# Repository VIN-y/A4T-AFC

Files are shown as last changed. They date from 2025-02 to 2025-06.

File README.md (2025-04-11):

[][cc-by-nc-sa]

# A4T-AFC: [A]nother [4]010 [T]oolhead - [A]nother [F]ilament [C]utter

## BETA Release

A toolhead cutter mod from: ko-fi (https://ko-fi.com/southash1) [SouthAsh1](https://ko-fi.com/southash1)

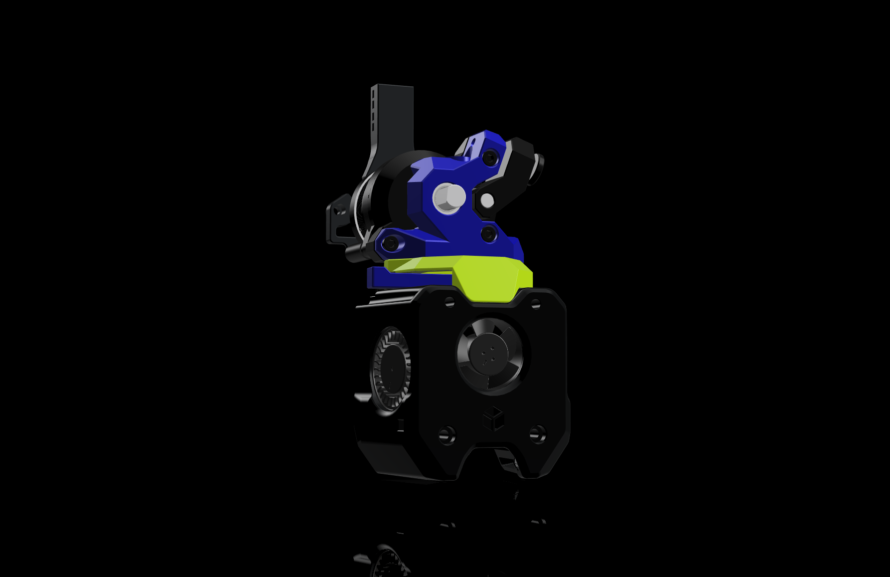
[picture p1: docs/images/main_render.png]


<br/> 
A filament cutter mod designed around the A4T that is designed by DW-Tas. Focused on keeping the original size as close as possible while still keeping the build relatively simple. <br/><br/>

I will try to get the board mounts made soon.

> [!NOTE] 
> ### Total WIP<br/>
> This mod is still a WIP and some things may change, most changes will be minor. Also the CAD will come out later.<br/>

<br/><br/>

> [!WARNING]
> ### Very Sharp  
> This project requires you to modify very sharp objects. I will cover how to handle these when I get to finishing the instalation instructions very soon. 

<br/>

## Bill of Materials (BOM)
***`*Not including stock A4T hardware`***
| Qty | Item | Notes |
| --- | --- | --- |
| 1 | Bambu Blade | This mod uses a Bambu Labs filament cutter blade that has been stripped of its plastic. <a href="https://us.store.bambulab.com/products/replacement-filament-cutter?_pos=1&_ss=r">Bambu Blade</a>|
| 1 | 0.5x4x15 Spring | Any spring that is 4mm in diameter and no longer than 15mm should work your milage may vary for cutting force needed.|
| 1 | M2 x 4 FHCS | Keeps the blade from sliding in and out.|
| 2 | M2 `Flange` Heatsets | This is the bread and butter of tolerances for the build. <br/> Recommended: ---<a href="https://www.digikey.com/en/products/detail/tri-star-industries-inc/HM20X157C/14205393">Digikey</a> <br/> Alternative: --------<a href="https://www.aliexpress.us/item/3256805733805809.html">Ali Express</a>|
| 2 | 3 x 10 mm pin | Pivot pins for the `Link`<br/> Example: <a href="https://www.amazon.com/uxcell-Stainless-Cylindrical-Support-Elements/dp/B07Y58VWDW?th=1">Amazon</a>|
| 2 | 3 x 12 mm pin | Pivot pins for the `Cutter Arm` and `Blade Holder`<br/> Example: <a href="https://www.amazon.com/uxcell-Stainless-Cylindrical-Support-Elements/dp/B07Y58CFYF?th=1">Amazon</a>|
| 4 | 3 ID x 5 OD x 5 H mm Sleeve Bearings | Bearing surfaces for the pins to guide on. <br/> Example: <a href="https://www.amazon.com/uxcell-Bearings-Wrapped-Bushings-Machinery/dp/B0CW31938R?th=1">Amazon</a>|
| 1 | M3 Threaded Heat Insert | Standard Voron spec: M3 x 5 x 4|
| 1 | M3 x 6 SHCS | Holds the `Extruder Adapter` on.|
| | **OPTIONAL** |
| 4 | M2.5 x 8 / M2.5 x 12 FHCS | To mount the hotend for ONLY the UHF options. 12mm length if you are using the spacer.|
| | **Extruder Mounting Screws** |
| | WWBMG, Orbiter | 2-`M3x18 SHCS`|
| | WWG2 | 1-`M3x20 SHCS` 1-`M3x18 SHCS`|
| | Sherpa | 2-`M3x24 BHCS` Sorry but you need to file/sand down 1mm on 25mm screws.|

## Printing parts
### Print settings
> [!WARNING]<br/>
> Recommended to print the `Link` and `Blade Holder` with 100% infill.<br/>

Parts are meant to be printed in 0.2mm layer heights, 0.25mm first layer should be OK. Other layer heights will cause the built-in supports to fail or fuse to the printed part.<br/>
Print settings will depend on your printer setup / filament used / phase of the moon/etc.<br/>
The parts are not pre-scaled for any particular filament type. You will need to tune the filament you use for correct shrinkage compensation to get good results. Development was done with multiple brands of ASA and ASA-CF filaments (each individually tuned).<br/>

General voron-like settings are a good starting point for 0.4mm wall widths (four walls, 5 top/bottom layers and 40% infill).<br/>

⚠ If you have any under-extrusion you will have problems with the parts stretching and not keeping rigidity. ⚠

(Similar rules of A4T applies here so I kind of copied and pasted, sue me...)

## Assembly
### Assembly Steps

These istructions should be followed in conjunction with original <a href="https://github.com/Armchair-Heavy-Industries/A4T">A4T instructions</a>.

:information_source: CW2 and Tap users have to build the toolhead on the printer, Xol Carriage users can build off the printer.
| <center>Notes</center> | Images|
| --- | :-----: |
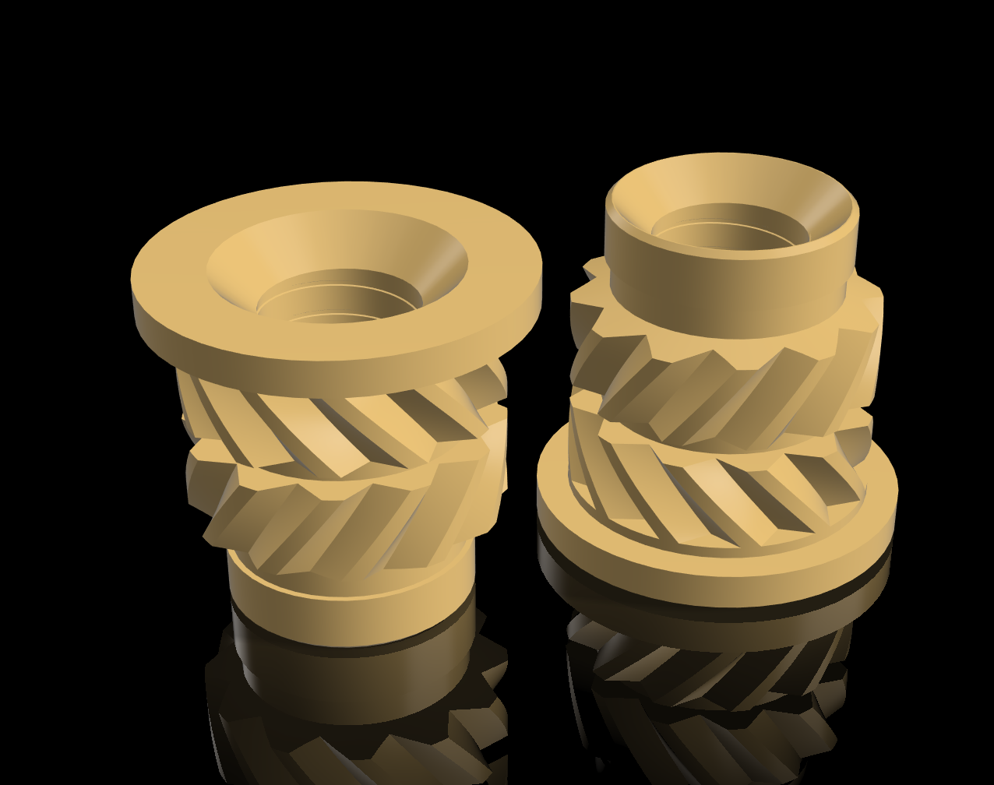
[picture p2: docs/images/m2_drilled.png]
| Prep the M2 inserts for install by drilling them out with a 5/64 or 2mm Drill Bit, then in one of them chamfer the top and the other chamfer the bottom. | <br/> |
| **Preping the Blade Holder** |
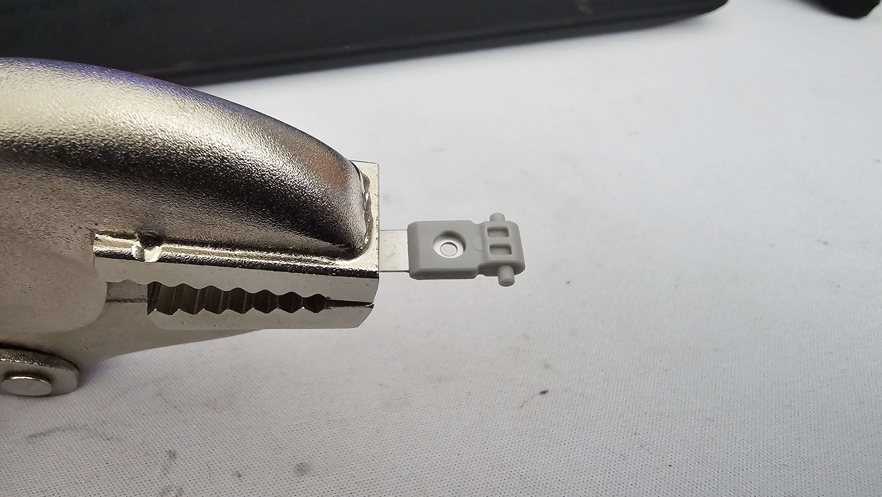
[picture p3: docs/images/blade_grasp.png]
| Start by using a pair of vise grips, a pair of pliars, or a vise that can firmly grasp the blade and prevent it from moving. | <br/> |
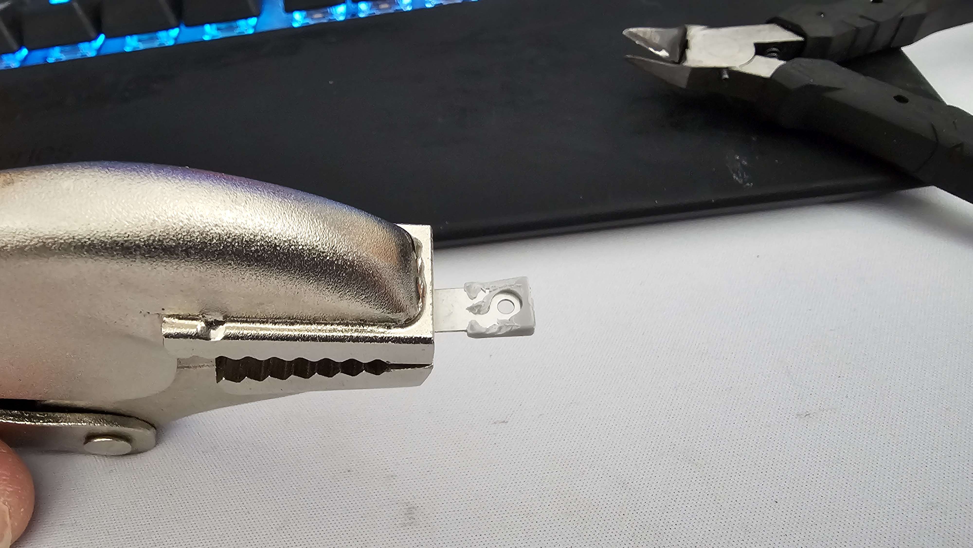
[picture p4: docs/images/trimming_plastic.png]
| Next, using flush cutters, cut the tab on the back `⚠⚠ flying parts ⚠⚠` and start triming the plastic off one side. | <br/> |
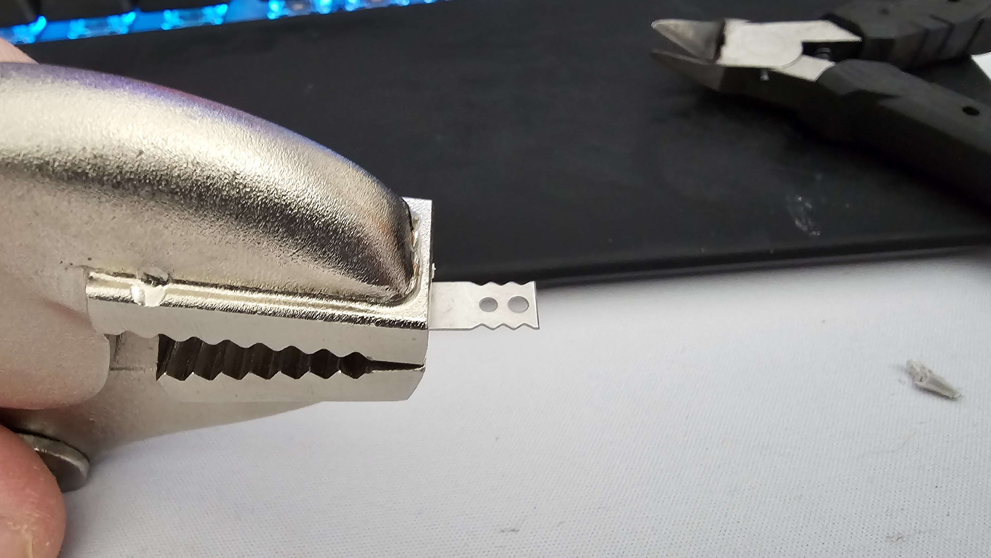
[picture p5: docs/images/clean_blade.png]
| When you get enough plastic off one side then the other side can just be pulled off then you will get a clean blade ready for install. | <br/> |
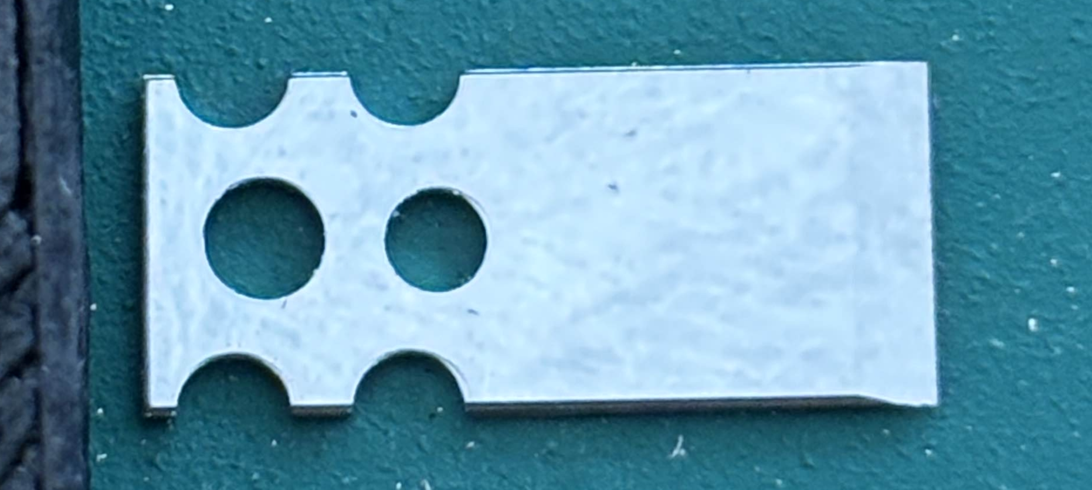
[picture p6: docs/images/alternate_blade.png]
| There are alternate types of Bambu blades that may differ depending on where on the globe you buy them on, they will still work. | <br/> |
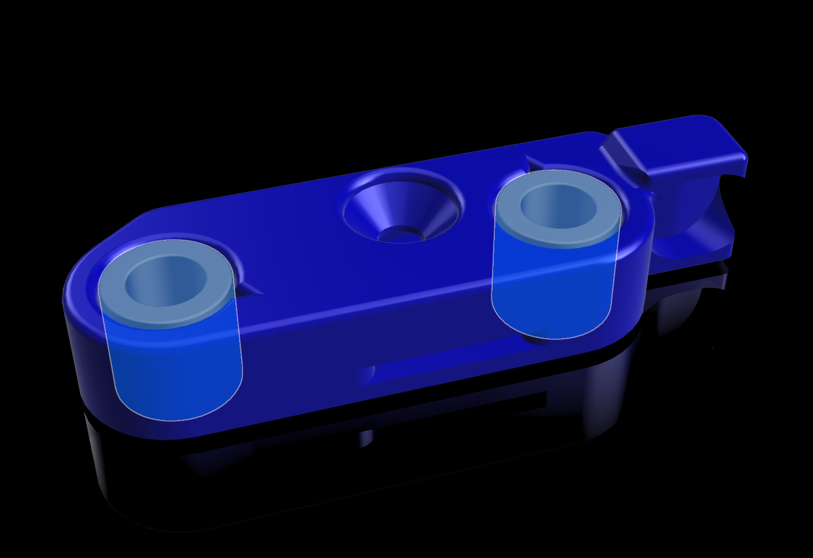
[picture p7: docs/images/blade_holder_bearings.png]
| Insert 2 of the `Sleeve Bearings` into the `Blade Holder` | <br/> |
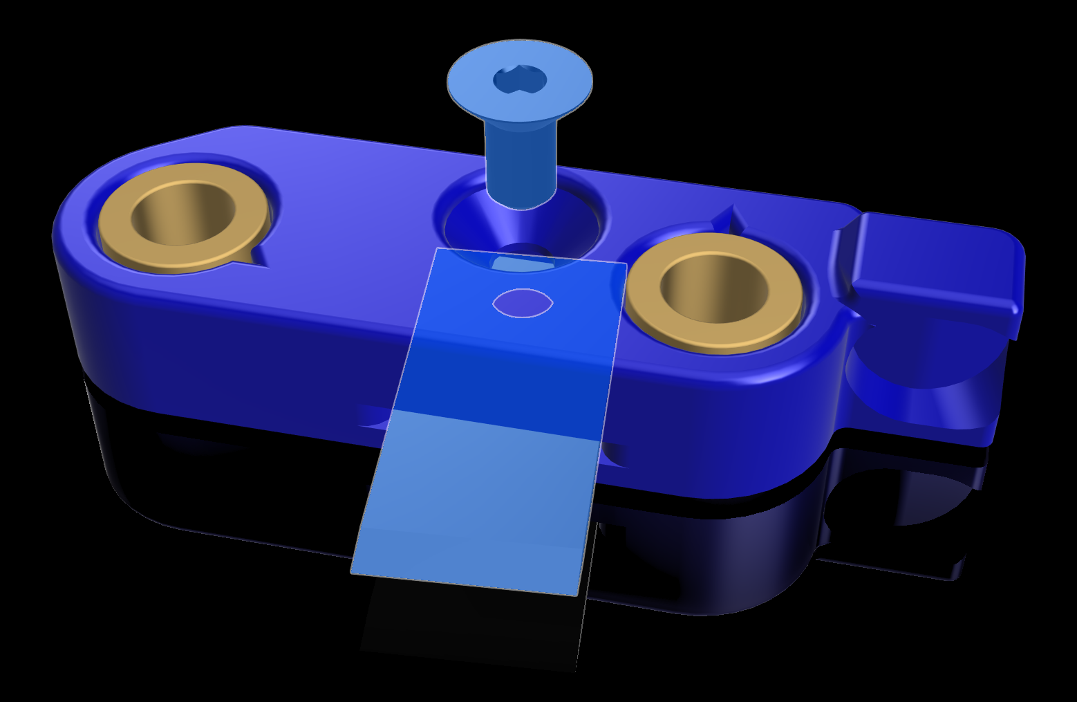
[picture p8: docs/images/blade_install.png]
| With the blade still in the vise grips, slide it into the Blade Holder. Install the M2 FHCS making sure you don't overtighten as it's going into plastic. | <br/> |
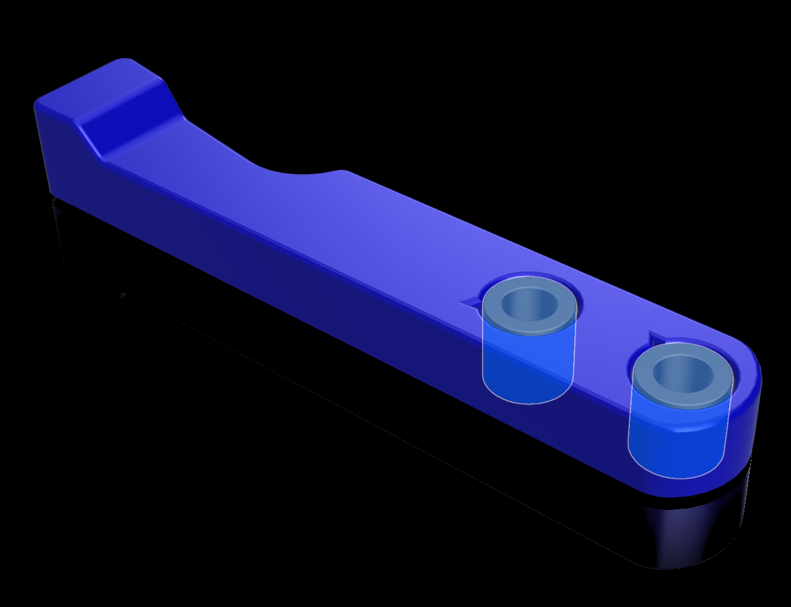
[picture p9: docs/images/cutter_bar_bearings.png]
| Insert the 2 remaining `Sleeve Bearings` into the `Cutter Bar` | <br/> |
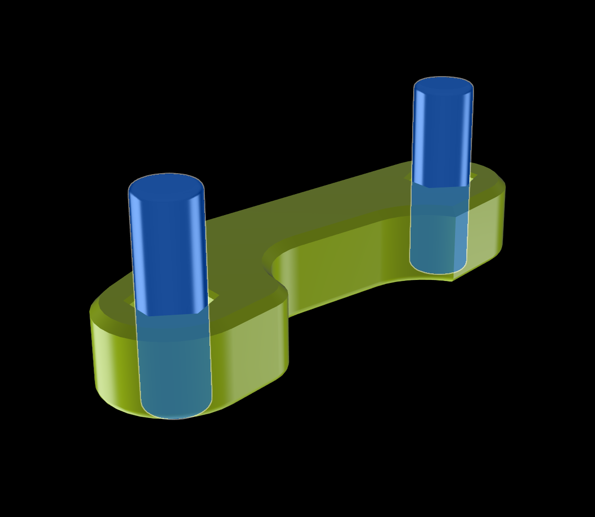
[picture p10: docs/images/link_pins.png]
| Insert the 2 `3x10mm Pins` into the `Link` the pins will stick out the top with 5mm coming out the bottom. Picture is showing the bottom of the link. | <br/> |
| **Preping the Extruder Adapter** |
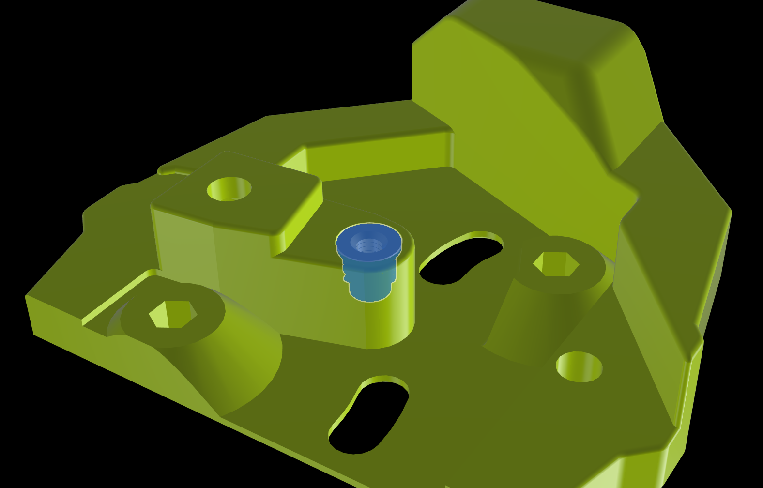
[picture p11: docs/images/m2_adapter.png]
| Install the M2 insert that is chamfered on the bottom into the Extruder Adapter. | <br/> |
| **Cutter Install** |
| Before installing, CW2 and Tap users need to install the cowl to the carriage now. |
| UHF users will need to use `M2.5x8/12 FHCS` to install the hotend. |
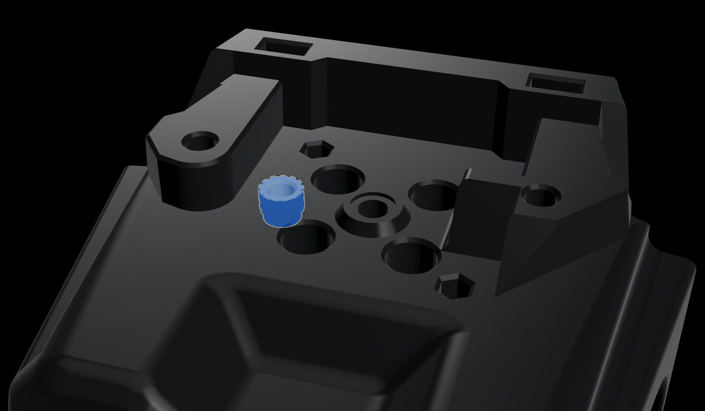
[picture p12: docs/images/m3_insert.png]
| Insert the M3 insert | <br/> |
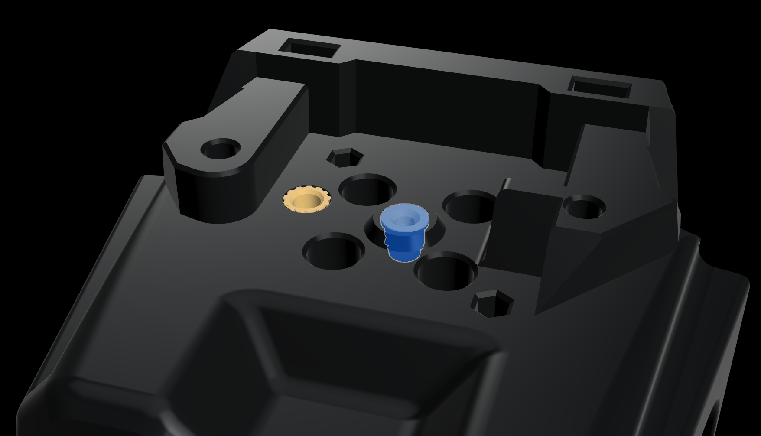
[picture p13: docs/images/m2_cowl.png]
| Insert the M2 insert that is chamfered on the top into the cowl making it flush with the surface. | <br/> |
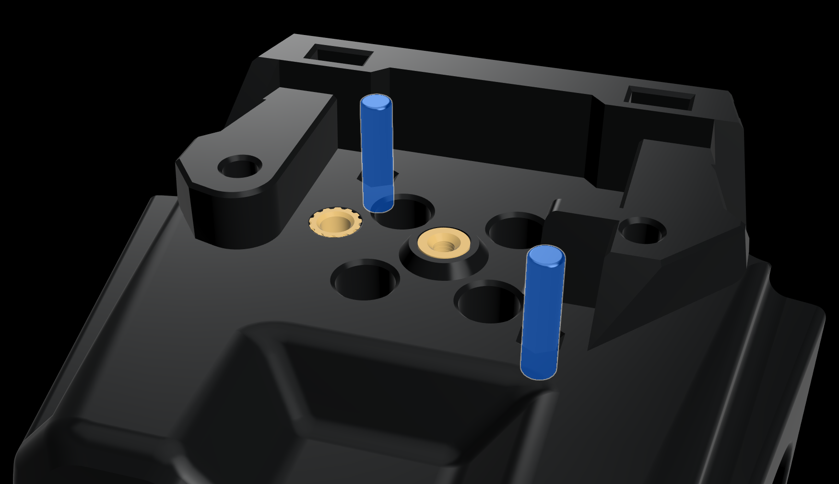
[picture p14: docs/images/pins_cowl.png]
| Insert the 2 `3x12mm Pins` into the cowl. | <br/> |
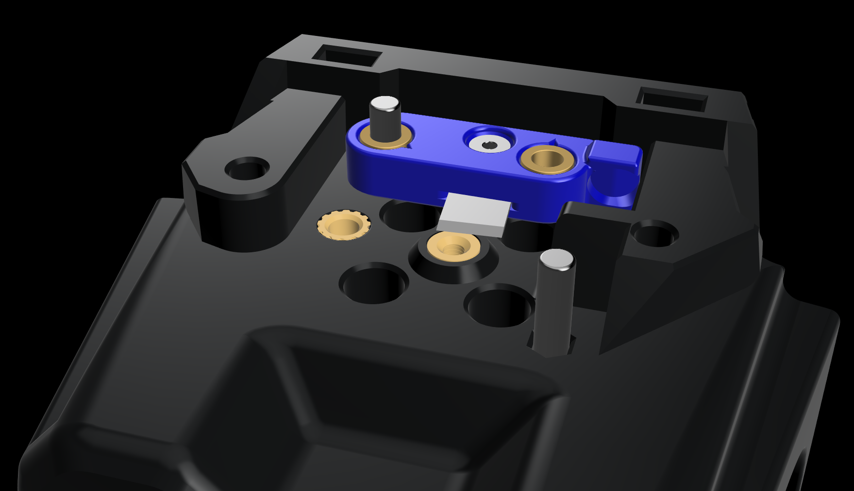
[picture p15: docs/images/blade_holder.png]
| Carefully install the `Blade Holder` | <br/> |
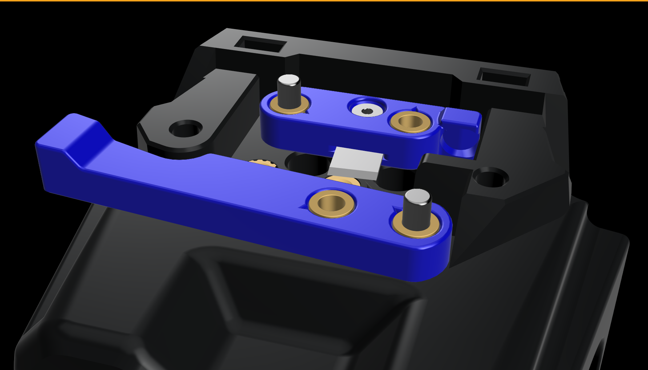
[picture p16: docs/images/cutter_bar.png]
| Install the `Cutter Arm` | <br/> |
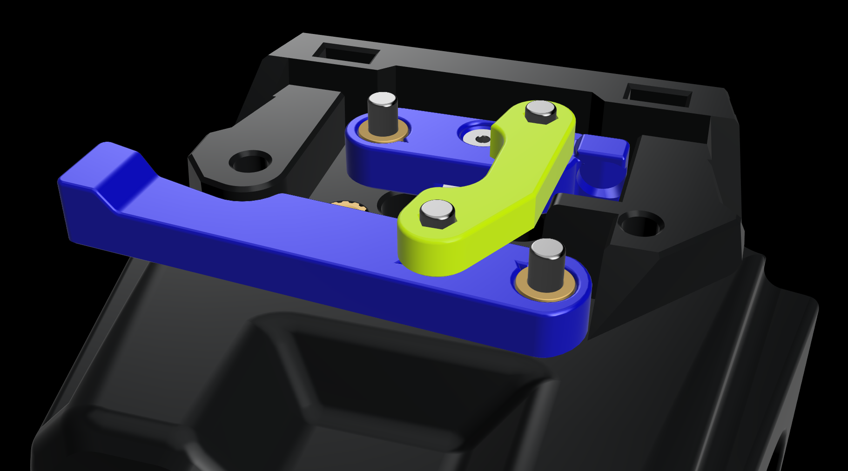
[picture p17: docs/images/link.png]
| Install the `Link` | <br/> |
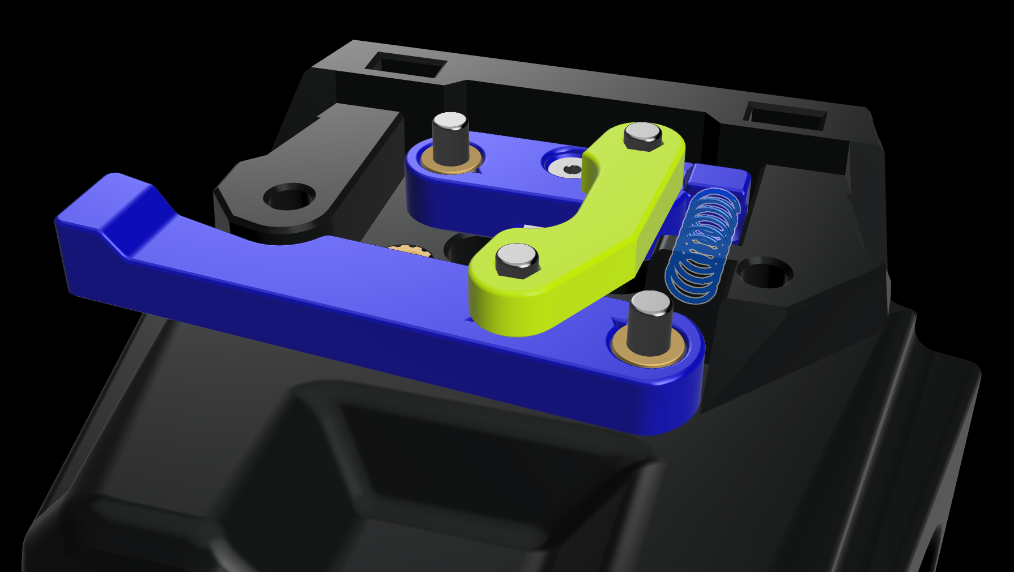
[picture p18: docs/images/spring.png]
| Using some tweasers install the spring, being sure to secure the ends into the holes. Test out the mechanism to make sure it resets with no binding. | <br/> |
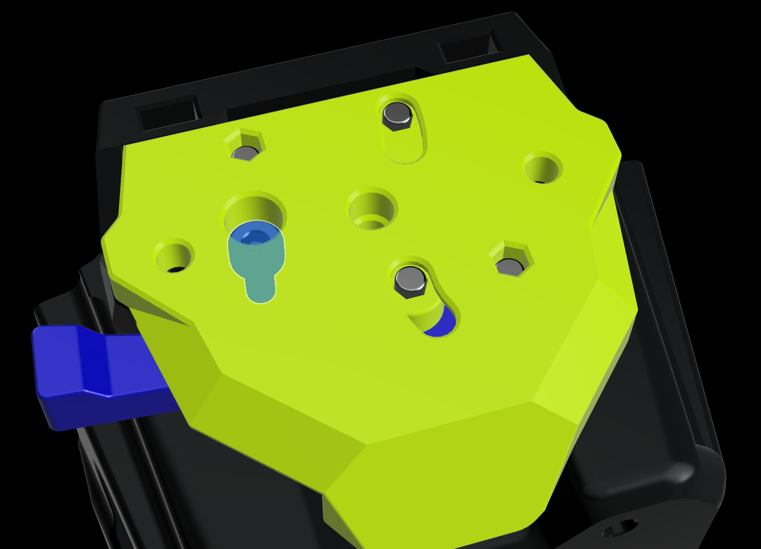
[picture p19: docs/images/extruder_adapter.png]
| Last the Extruder adapter can be installed and secured with an `M3x6 SHCS`. The rest of A4T instructions can be continued. | <br/> |

<br>

### 

### Credits
* Thanks to everyone that supported my last project/mod.
* Thanks to DW-Tas for all the help provided and for designing <a href="https://github.com/Armchair-Heavy-Industries/A4T">A4T</a>.

Go support the guys over at <a href="https://github.com/Armchair-Heavy-Industries">Armchair Heavy Industries</a> as they are making some awesome stuff over there!

## Enjoy using A4T-AFC
This work is licensed under a
[Creative Commons Attribution-NonCommercial-ShareAlike 4.0 International License][cc-by-nc-sa].

[][cc-by-nc-sa]

[cc-by-nc-sa]: http://creativecommons.org/licenses/by-nc-sa/4.0/
[cc-by-nc-sa-image]: https://licensebuttons.net/l/by-nc-sa/4.0/88x31.png
[cc-by-nc-sa-shield]: https://img.shields.io/badge/License-CC%20BY--NC--SA%204.0-lightgrey.svg

### License clarification regarding non-commercial use:
The non-commercial aspect of this license is for cases where A4T is the product, not the use of A4T to create products.<br/>
I.e. If you wish to sell A4T as a product, you would need to seek a commercial license before doing so. </br>
It is NOT intended to prevent the use of A4T in a printer that you use to provide commercial services. If you want to run A4T as a toolhead for your print farm printers, go right ahead.

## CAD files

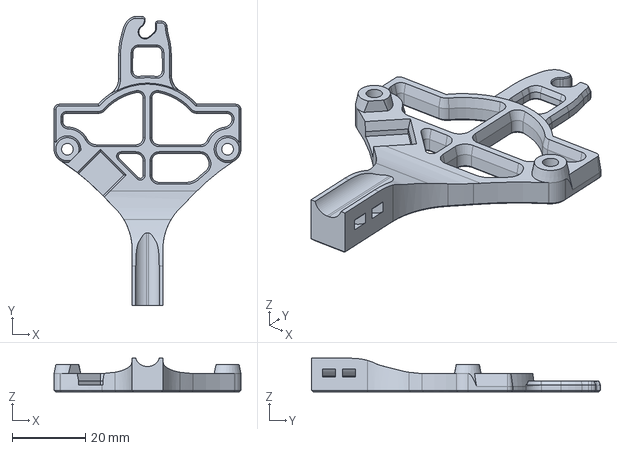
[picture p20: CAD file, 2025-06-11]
CAD/THB Mounts/Sherpa Board Mount.step
51.2 x 79.1 x 9.20 mm

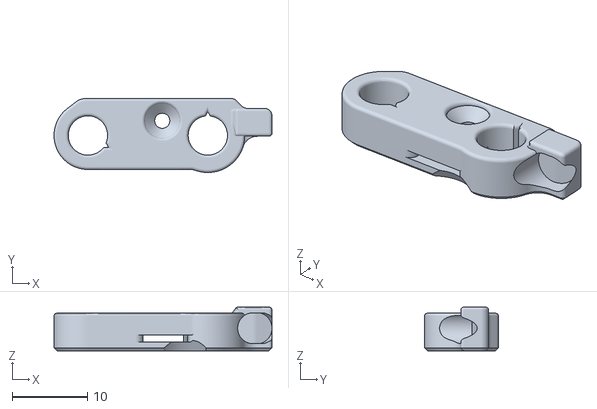
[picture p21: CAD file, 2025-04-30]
STL/Blade Holder.stl
28.9 x 9.80 x 5.80

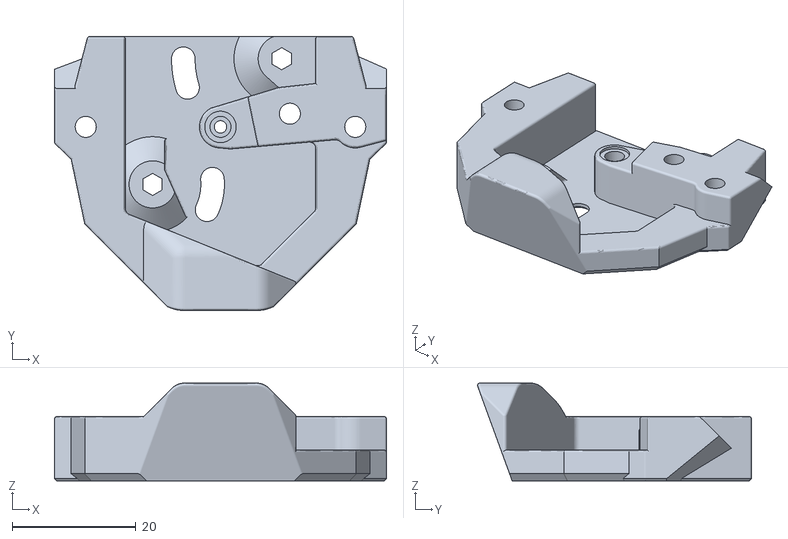
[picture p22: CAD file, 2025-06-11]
STL/Extruder Adapters/A4T - Extruder Adapter - Sherpa.stl
53.6 x 44.2 x 15.8

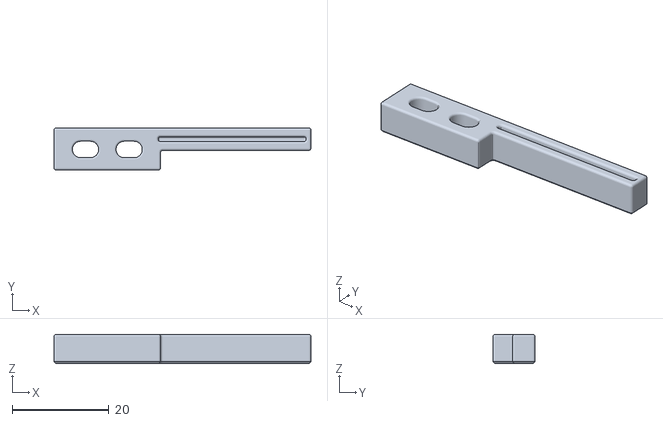
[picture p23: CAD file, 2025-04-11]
STL/Gantry Arm/Depressor Arm.stl
53.0 x 8.68 x 6.00

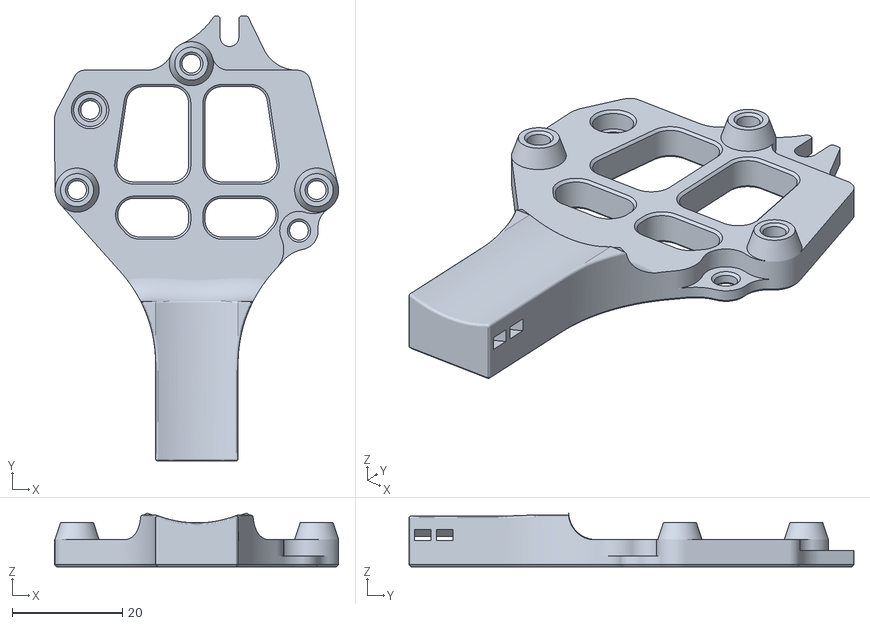
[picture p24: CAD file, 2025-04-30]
STL/THB Mounts/A4T - THB Mount - Orbiter v2.0.stl
51.7 x 80.8 x 9.73

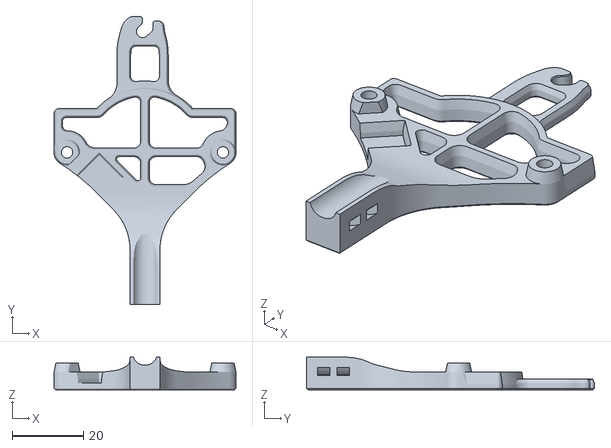
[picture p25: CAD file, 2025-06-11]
STL/THB Mounts/UHF/A4T - THB Mount - Sherpa-Mini UHF.stl
51.2 x 81.0 x 9.20

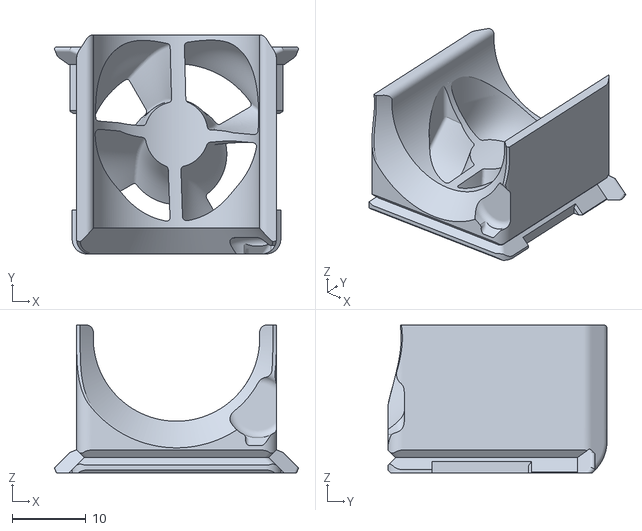
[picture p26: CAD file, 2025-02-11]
STL/UHF Fan Ducts/A4T HE Fan Duct - Rapido.stl
33.0 x 29.6 x 20.0

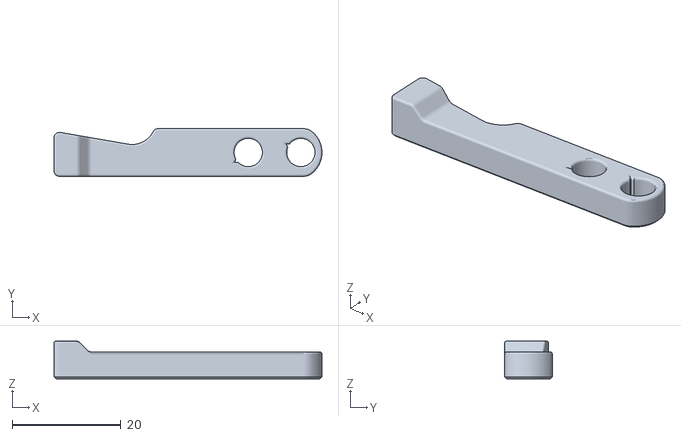
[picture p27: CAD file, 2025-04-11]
STL/Cutter Bar.stl
49.4 x 8.80 x 7.00

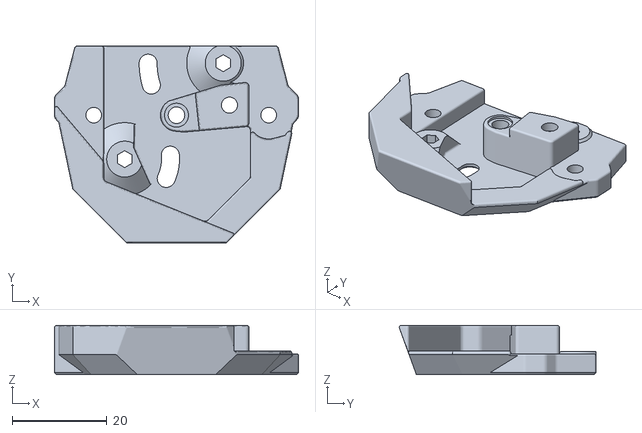
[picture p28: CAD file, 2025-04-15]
STL/Extruder Adapters/A4T - Extruder Adapter UHF - Orbiter G2.stl
51.6 x 41.6 x 10.4

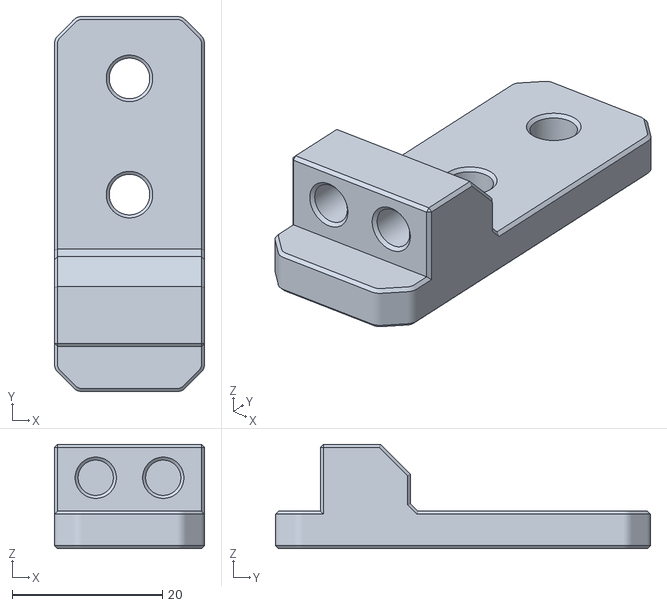
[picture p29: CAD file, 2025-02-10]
STL/Gantry Arm/Depressor Arm Base.stl
20.0 x 50.0 x 13.9

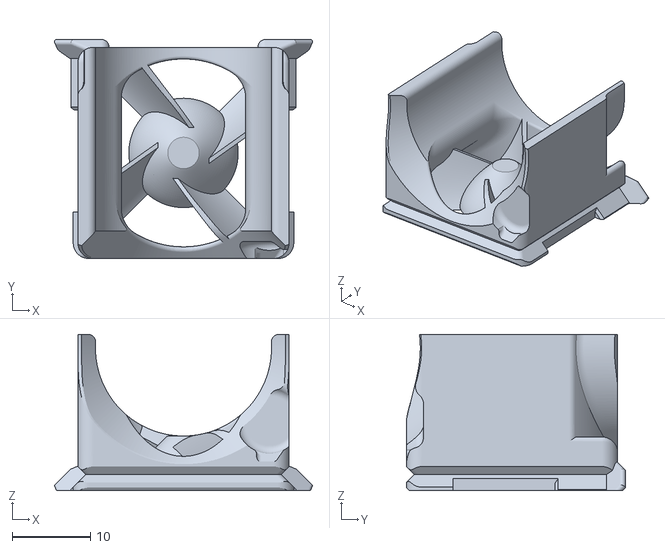
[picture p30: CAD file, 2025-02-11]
STL/UHF Fan Ducts/A4T HE Fan Duct - Dragon.stl
33.0 x 28.0 x 20.0

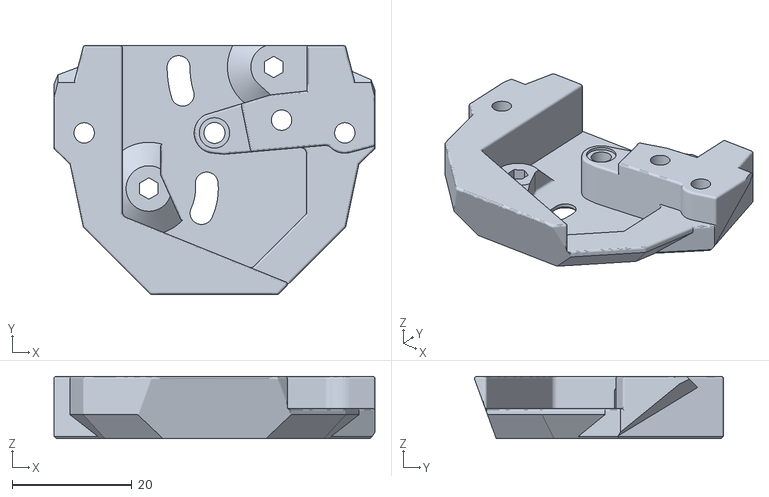
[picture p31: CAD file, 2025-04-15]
STL/Extruder Adapters/A4T - Extruder Adapter UHF - Sherpa.stl
53.6 x 41.6 x 10.4

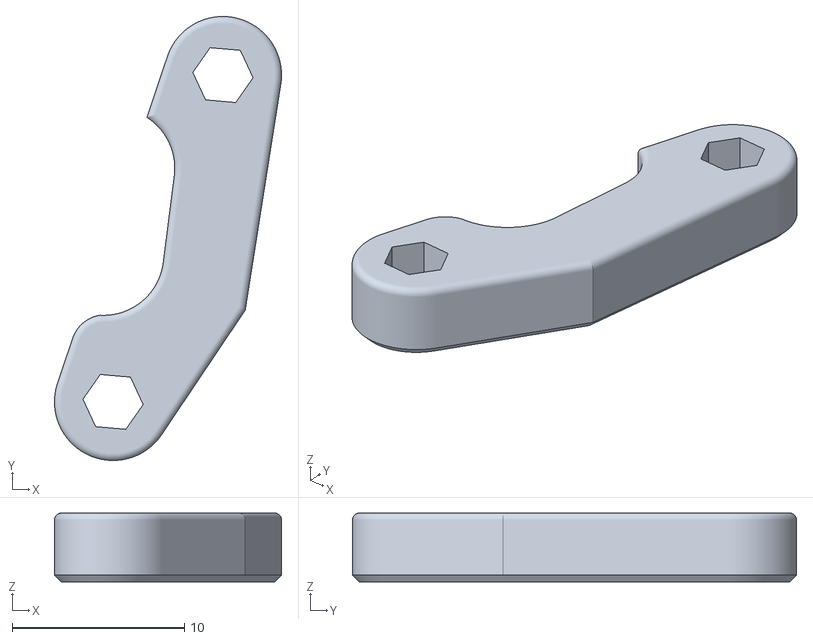
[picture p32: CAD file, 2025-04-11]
STL/Link.stl
13.2 x 25.8 x 4.00

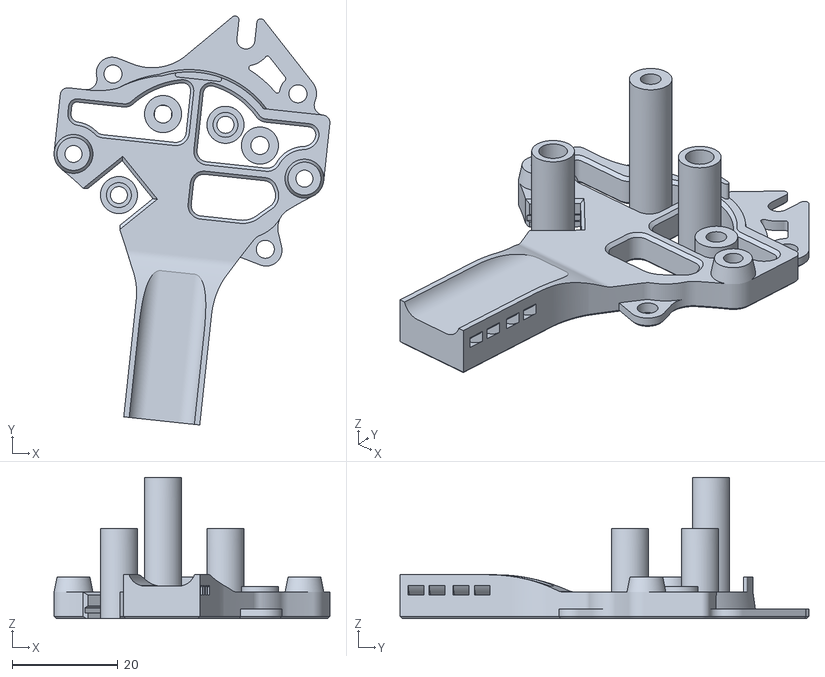
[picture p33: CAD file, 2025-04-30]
STL/THB Mounts/A4T - THB Mount - WWG2.stl
52.1 x 77.2 x 26.6

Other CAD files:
STL/THB Mounts/A4T - THB Mount - Sherpa-Mini.stl
STL/THB Mounts/UHF/A4T - THB Mount - Orbiter v2.0 UHF.stl
STL/THB Mounts/UHF/A4T - THB Mount - WWG2 UHF.stl
STL/Extruder Adapters/A4T - Extruder Adapter - Orbiter G2.stl
STL/THB Mounts/A4T - THB Mount - WWBMG.stl
STL/THB Mounts/UHF/A4T - THB Mount - WWBMG UHF.stl

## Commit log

2025-02-10 BIG update
    [Depressor Arm Base.stl, Depressor Arm.stl]
2025-02-11 small updates
    [A4T HE Fan Duct - Dragon.stl, A4T HE Fan Duct - Rapido.stl]
2025-02-14 Updates
    updated cowls, added TZ-V6 cowls, and added install instructions v1
    [A4T - Extruder Adapter UHF - Sherpa.stl, A4T Cowling - Dragon-Rapido UHF - G2-Orb Spacing [cw2-tap].3mf]
2025-02-15 Update A4T Cowling - Dragon_Rapido [xol-carriage].stl
2025-02-15 Update Blade Holder.stl
    [Blade Holder.stl]
2025-02-19 update tiiiime!
    -got rid of the bridge part and integrated it with the extruder adapter
    -made the blade in the holder strait to make it extend out slightly more
    -added a .5mm shorter link for anyone that needs it
    -updated photos accordingly
    [A4T - Extruder Adapter - Orbiter G2.stl, A4T - Extruder Adapter - Sherpa.stl, A4T - Extruder Adapter UHF - Orbiter G2.stl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]
2025-02-22 mainly updated link
    [A4T - Extruder Adapter - Orbiter G2.stl, A4T - Extruder Adapter - Sherpa.stl, A4T - Extruder Adapter UHF - Orbiter G2.stl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]
2025-04-11 New Update!
    Updated parts to be more reliable and much more smooth in action.
    [A4T - Extruder Adapter - Orbiter G2.stl, A4T - Extruder Adapter - Sherpa.stl, A4T - Extruder Adapter UHF - Orbiter G2.stl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]
2025-04-15 Small Error
    [A4T - Extruder Adapter UHF - Orbiter G2.stl, A4T - Extruder Adapter UHF - Sherpa.stl]
2025-04-30 Blade holder beefy
    [A4T - THB Mount - Orbiter v2.0.stl, A4T - THB Mount - Sherpa-Mini.stl, A4T - THB Mount - WWBMG.stl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]
2025-06-11 Added some THB mounts
    Added these THB mounts
    -Sherpa Mini UHF
    -WWG2 UIHF
    -Orbiter 2.0 UHF
    -WWBMG UHF
    [A4T - Extruder Adapter - Sherpa.stl, A4T - THB Mount - Orbiter v2.0 UHF.stl, A4T - THB Mount - Sherpa-Mini UHF.stl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]
2025-06-11 View Update
    Updated some cowls to match the update to the nozzle view port.

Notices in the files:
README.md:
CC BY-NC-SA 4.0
